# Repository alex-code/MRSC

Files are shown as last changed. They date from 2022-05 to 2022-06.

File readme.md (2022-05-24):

# **M**odel **R**ailway **S**ervo **C**ontroller

Control points, semaphore signals and other accessories using servos.

A demo video can be found here, https://www.youtube.com/watch?v=__FOfBjZpas

| :warning: | I'm a C++ hobbyist (Not a pro) and this is a personal project I've shared that will require some tinkering knowledge. While this has worked for me results may vary and you might need to modify the code.| :warning: |
|--|--|--|

| :information_source: | This was developed using Visual Studio Code and PlatformIO but should be Arduino IDE compatible. | :information_source: |
|--|--|--|

There's 4 types that have different options
- Point - Has 4 speed options
- Semaphore Signal - Can simulate drop bounce and pull up hesitation
- Sweep - Has 4 speed options (Can be used for gates)
- On\Off - Can be used with N Channel mosfets

Parts:
- Arduino UNO
- LCD Keypad Shield (16x2) (I used this https://www.dfrobot.com/product-51.html)
- MCP23017 I/O Port Expander (I used these https://www.dfrobot.com/product-2002.html)
- PCA9685 PWM Servo Driver

Switches can be ON-ON or ON-OFF, they just need to be latching.

I used SG90 servos as they're cheap and common.

## Config

By default the code is setup to handle 4 MCP23017 boards (addressed as 0x20, 0x21, 0x22 & 0x23) and 4 PCA9685 boards (addressed as 0x40, 0x41, 0x42, 0x43).

If the Keypad you have doesn't work you'll need to check the resistance values as these may vary between manufactures.

# Wiring

To make a simpler install I used MCP23017 & PCA9685 boards with pre-soldered headers.

The MCP23017 expanders are set to input pullups so switches need connecting to GND and one of the input pins.

Unless your boards have DIP switches to change the I2C addresses you'll need to do a bit of soldering.

The boards can then be chained with the SDA & SCL pins on the Uno.

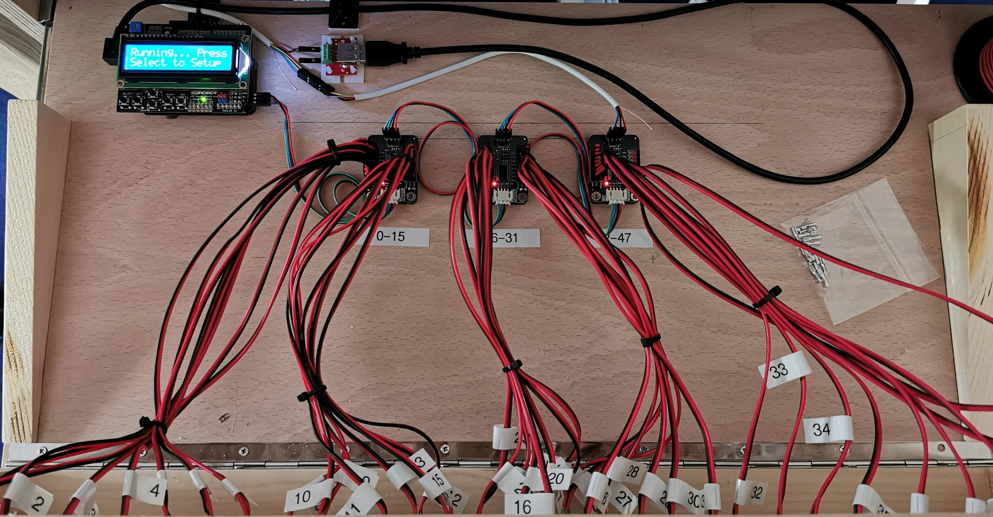
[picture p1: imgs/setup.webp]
My setup


# Servo Numbering

Boards are paired by the order of the addresses in the array.
e.g
```cpp
// MCP's
const uint8_t MCP_ADDRESSES[BOARD_COUNT] = { 0 /* 0x20 */, 1 /* 0x21 */ };
// PCA's'
const uint8_t PCA_ADDRESSES[BOARD_COUNT] = { 0x40, 0x41 }; 
```
The first `MCP` and `PCA` pair will be 0-15 and the second  pair will be 16-31.

# Servo Setup

Servos are a little tricky to setup as the position is unknown to the controller so you'll need to center the servo first (minus the control arm).

- Press *SELECT* on the keypad to start setup.
- You'll first be prompted to select the servo number, use the *UP*/*DOWN* buttons to scroll through the numbers. Press *SELECT* to confirm.
- Press *SELECT* on the first option **Setup/Change**.
- The type can now be selected, **Point**, **Semaphore**, **Sweep**, or **On\Off**. Use the *UP*/*DOWN* buttons to go through the menu options and press *SELECT* on the type you want.
- The servo will now centre.
- After centring you can now fit the arm and the piano wire.
  - For points the arm should be vertical.
  - For semaphore signals the arm should be horizontal.
- You can now set the limits, use the *LEFT*/*RIGHT* buttons to jog the servo in the first direction. When happy with the amount of pressure press *SELECT*. Now go in the opposite direction to set the second limit. Press *SELECT* to confirm.
- You'll then be prompted if the limits are correct. The switch can be toggled at this stage to test, if they are then just press *SELECT* otherwise using the *UP*/*DOWN* buttons you can scroll to **No** and press *SELECT* to go through the limit setup again.
- You'll now be prompted if you want to change the direction the servo operates with the switch. Use *UP*/*DOWN* to change and press *SELECT* to confirm.
- **Point Type**
  - You can now select 1 of 4 speeds. Use the *UP*/*DOWN* buttons to scroll through the speeds. The switch can also be tested so you can give each speed a try. Press *SELECT* to confirm.
- **Semaphore Type**
  - Select if you want to simulate a semaphore signal bounce on drop. You can use the switch the test. Press *SELECT* to confirm.
  - Select if you want to simulate a semaphore hesitate on pull up. You can use the switch the test. Press *SELECT* to confirm.
- **Sweep Type**
  - You can now select 1 of 4 speeds. Use the *UP*/*DOWN* buttons to scroll through the speeds. The switch can also be tested so you can give each speed a try. Press *SELECT* to confirm.
- The display will then read **Setup Complete** before prompting if you want to setup another servo.
If you select **Yes** the servo select will auto increment to the next number so you can just press *SELECT* to continue or use the *UP*/*DOWN* buttons to select a different servo.

## Existing
If you need to change an existing servo.
- Press *SELECT* on the keypad to start setup.
- You'll first be prompted to select the servo number, use the *UP*/*DOWN* buttons to scroll through the numbers. Press *SELECT* to confirm.
- Press *SELECT* on the first option **Setup/Change**.
- If the servo has a previous setup you'll be prompted if you want to overwrite. This allows you to change the type and reset the limits.
- Depending on the type you'll then be able to change the options.

# Servo Mounts

Servos can be mounted with which ever method suits you best but I've included some STL files that can be used to 3D print underside and topside servo mounts (underside needs a 10mm hole for the shaft).

| :warning: | I model in N Gauge so they're sized for that, if you plan on using them for OO/HO they may need tweaking | :warning: |
|--|--|--|

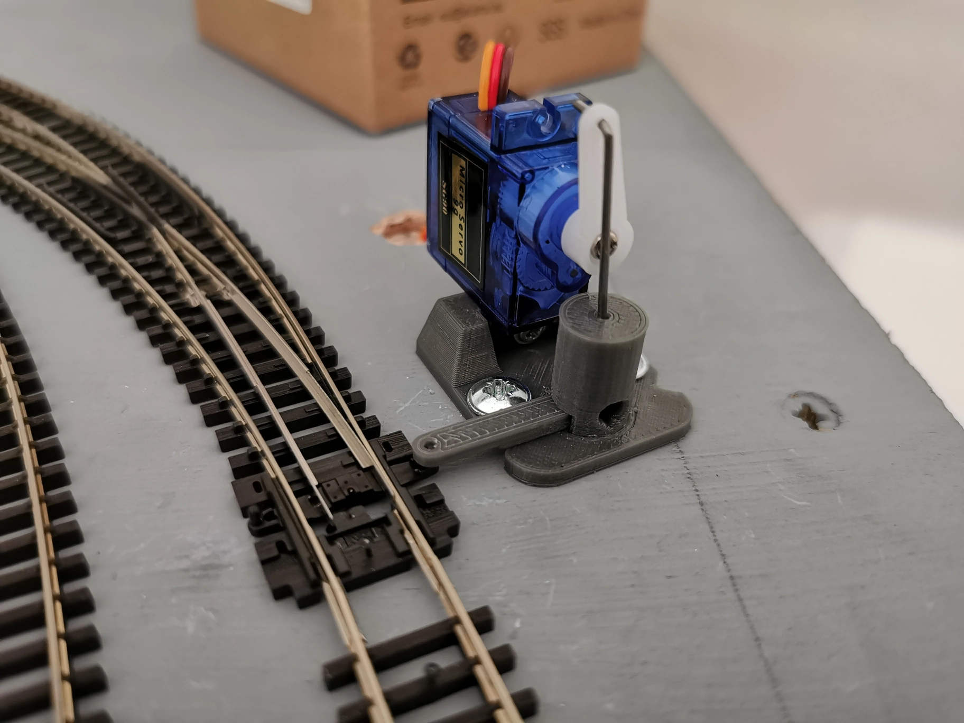
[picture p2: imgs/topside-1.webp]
Topside mount

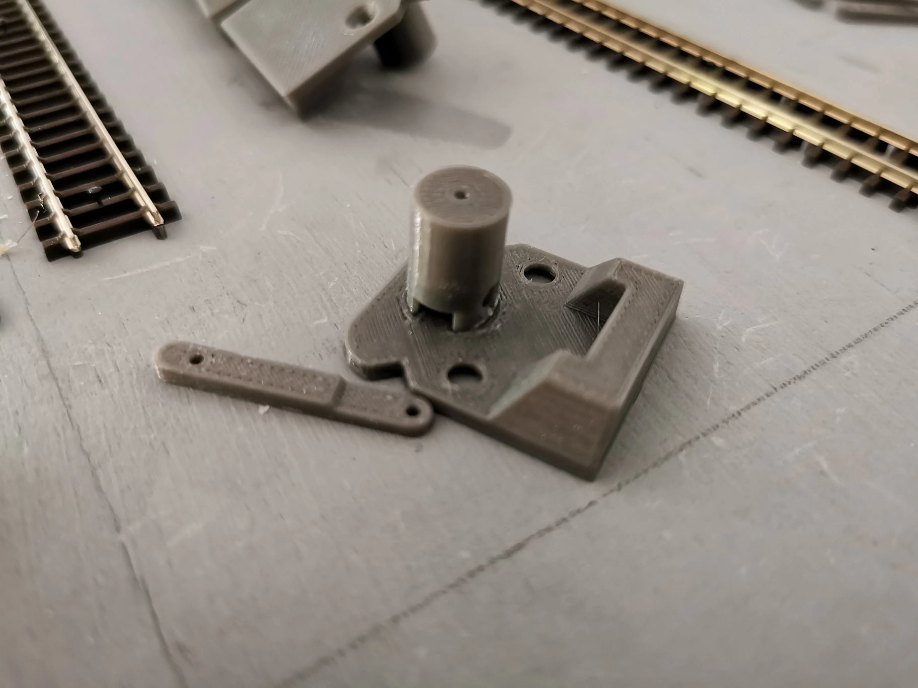
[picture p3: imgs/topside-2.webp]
Topside mount

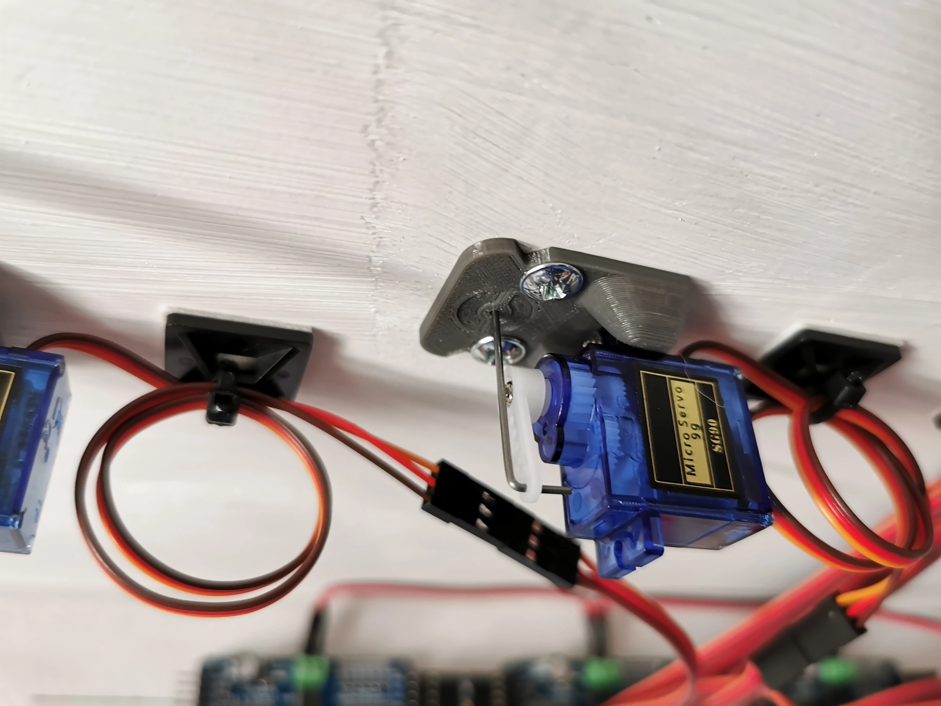
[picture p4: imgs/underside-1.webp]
Underside mount

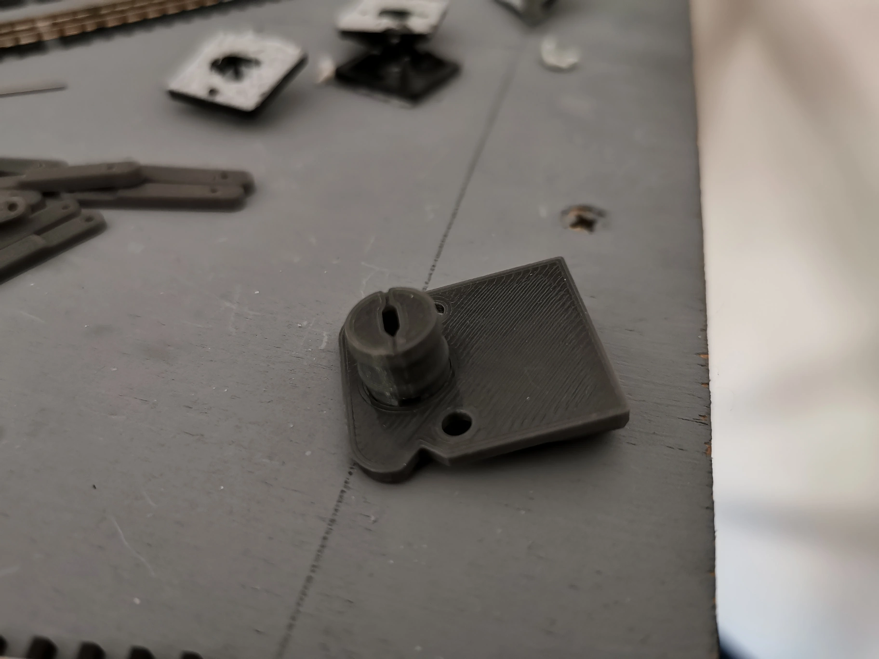
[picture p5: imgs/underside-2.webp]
Underside mount


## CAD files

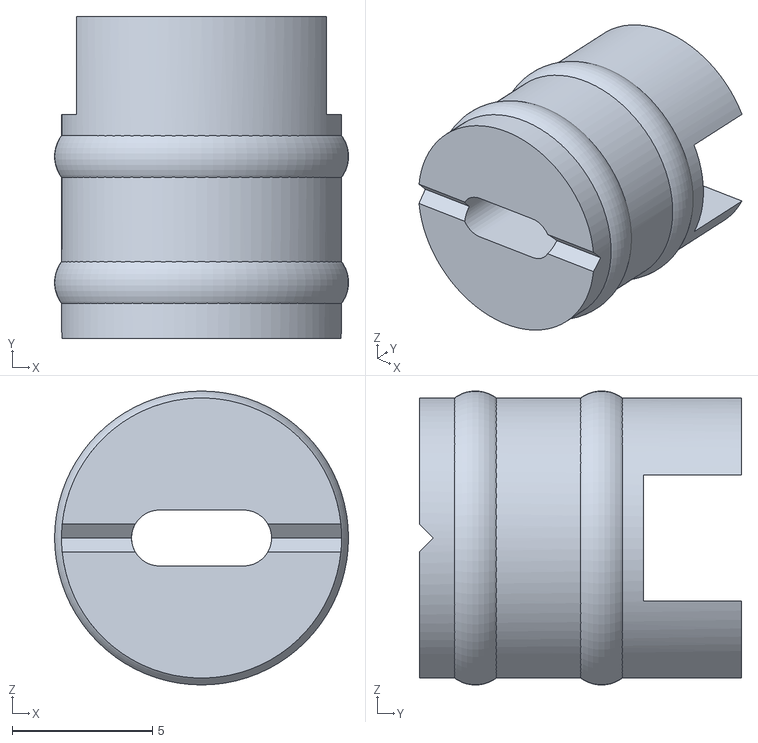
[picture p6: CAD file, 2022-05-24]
3d/Underside Shaft.stl
10.5 x 11.5 x 10.5

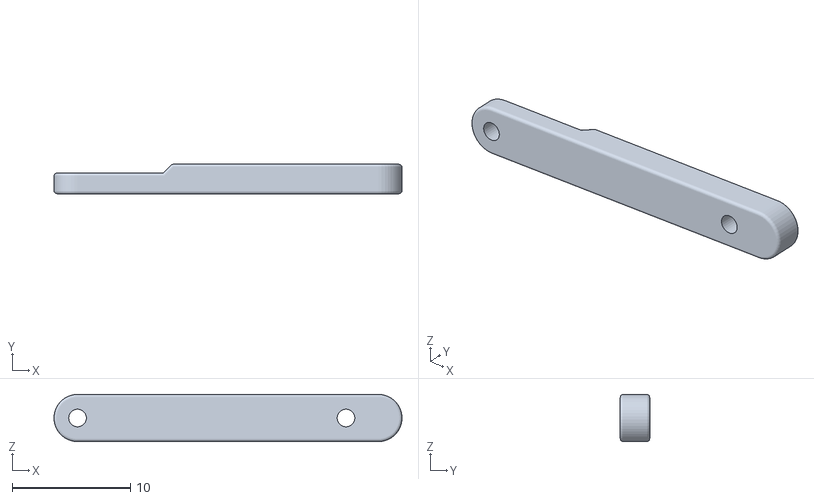
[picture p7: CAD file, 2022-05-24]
3d/Topside Rod.stl
29.5 x 2.50 x 4.00

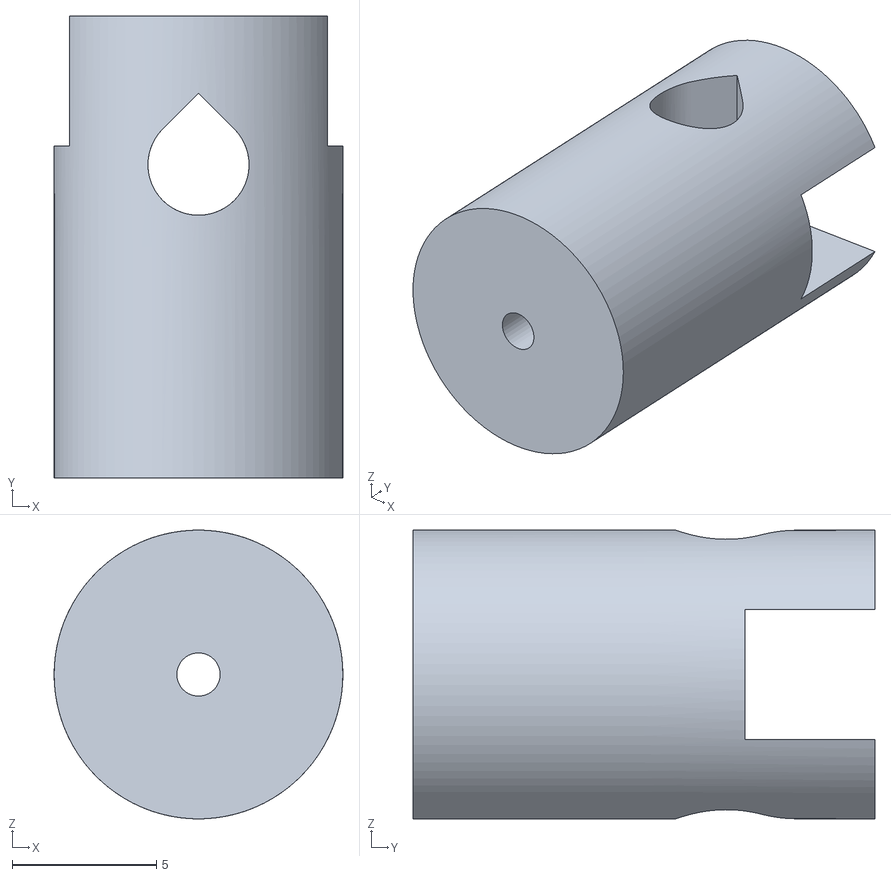
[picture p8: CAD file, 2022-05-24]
3d/Topside Shaft.stl
10.0 x 16.0 x 10.0

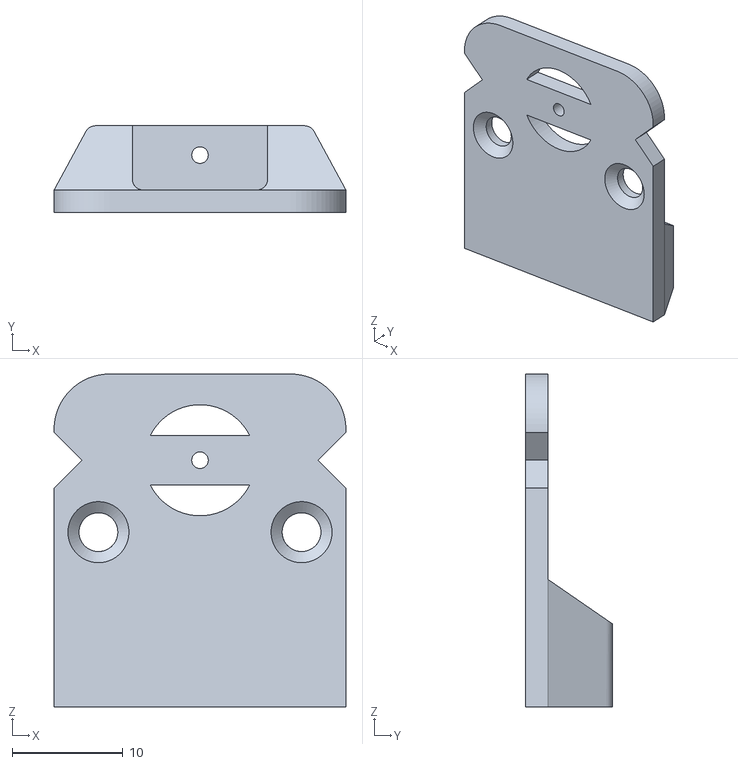
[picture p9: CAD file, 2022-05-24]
3d/Servo Mount.stl
26.3 x 7.80 x 30.0

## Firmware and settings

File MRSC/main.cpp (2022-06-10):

#include <Arduino.h>
#include <EEPROM.h>
#include <Wire.h>
#include <LiquidCrystal.h>
#include <Adafruit_MCP23017.h>
#include <Adafruit_PWMServoDriver.h>

// How many MCP23017 & PCA9685 boards are connected, needs to be an equal amount
const uint8_t BOARD_COUNT = 4;

// Keypad & Display
const uint8_t KEYPAD_PIN = 0; // A0

// MCP's - Addresses start from the base 0x20
const uint8_t MCP_ADDRESSES[BOARD_COUNT] = { 0 /* 0x20 */, 1 /* 0x21 */, 2 /* 0x22 */, 3 /* 0x23 */ };

// PCA Servo Drivers
const uint16_t SERVO_MIN = 90;
const uint16_t SERVO_MAX = 440;
const uint8_t SERVO_FREQ = 50;
const uint8_t PCA_ADDRESSES[BOARD_COUNT] = { 0x40, 0x41, 0x42, 0x43 };

// Board group
struct {
  Adafruit_MCP23017 *mcp = nullptr; // MCP23017
  Adafruit_PWMServoDriver *pca = nullptr; // PCA9685
  uint16_t states = 0;
} boards[BOARD_COUNT];

enum class Type : uint8_t {
  POINT,      // Full sweep from limit to limit
  SEMAPHORE,  // Full sweep from limit to limit with optional simulation of semaphore drop bounce and pull up hesitate
  SWEEP,      // Similar to POINT but with different speeds, can be used for gates etc.
  ONOFF       // 0v or 5v to allow trigger of other components, e.g N-Channel MOSFET
};

// These are ms delay times between each degree move
uint8_t pointSpeeds[] = { 25, 30, 35, 40 };
uint8_t sweepSpeeds[] = { 15, 25, 35, 45 };

// Servo config
struct {
  uint8_t limit1; // Limit 1
  uint8_t limit2; // Limit 2
  Type type;
  bool swap; // A convenience option, can swap the direction without needing to change wires
  uint8_t speed;
  bool hesitate; // Simulate hesitate
  bool bounce; // Simulate bounce
  uint32_t unused; // Bit of space in case there's future updates
} servos[BOARD_COUNT * 16];

#define MENUSIZE(items) sizeof(items) / 16
const char yesNoMenu[][16] PROGMEM = { "Yes", "No" };
const char servoSetupMenu[][16] PROGMEM = { "Setup/Change", "Swap Direction", "Centre", "Cancel" };
const char servoSetupTypeMenu[][16] PROGMEM = { "Point", "Semaphore", "Sweep", "On/Off" };
const char servoPointSpeedMenu[][16] PROGMEM = { "Speed 1", "Speed 2", "Speed 3", "Speed 4" };
const char servoSweepSpeedMenu[][16] PROGMEM = { "Speed 1", "Speed 2", "Speed 3", "Speed 4" };

uint8_t board = 0;
uint8_t pin = 0;
void checkForChange();

namespace Keypad {
  enum class Key : uint8_t {
    NONE    = 0,
    LEFT    = 1,
    RIGHT   = 2,
    UP      = 3,
    DOWN    = 4,
    SELECT  = 5
  };

  Key getKey(bool blocking = true) {
    Key key = Key::NONE;
    uint16_t adc;

    do {
      adc = 0;
      for (uint8_t i = 0; i < 5; i++) {
        adc += analogRead(KEYPAD_PIN);
        delay(5);
      }
      adc /= 5;

      if (adc < 50) {
        key = Key::RIGHT;
      } else if (adc < 250) {
        key = Key::UP;
      } else if (adc < 450) {
        key = Key::DOWN;
      } else if (adc < 650) {
        key = Key::LEFT;
      } else if (adc > 800 && adc < 850) {
        key = Key::SELECT;
      }
    } while (blocking && adc < 1000);

    return key;
  }
}

namespace Display {
  LiquidCrystal LCD(8, 9, 4, 5, 6, 7);

  void initialize() {
    LCD.begin(16, 2);
  }

  auto _change = [](int8_t) { };
  template<typename onChange = decltype(_change)>
  uint8_t showMenu(const __FlashStringHelper *title, const char menu[][16], uint8_t count, int8_t index = 0, onChange change = _change) {
    Keypad::Key oldKey = Keypad::Key::SELECT;
    Keypad::Key newKey = Keypad::Key::NONE;

    count--;
    if (index > count) {
      index = count;
    }

    LCD.clear();
    LCD.print(title);
    LCD.setCursor(0, 1);
    LCD.print((__FlashStringHelper*)&menu[index]);

    uint8_t len = strlen_P((const char*)title);
    int8_t scroll = len - 16;
    uint32_t wait = millis() + 1000;
    uint8_t i = 0;
    bool ltr = true;

    delay(100);

    do {
      if (len > 16 && millis() > wait) { // Scroll the title
        ltr ? i++ : i--;
        if (i == scroll || i == 0) { // Change scroll direction
          ltr = !ltr;
          wait = millis() + 1000; // Wait for 1 second before starting to scroll again
        } else {
          wait = millis() + 500;
        }
        
        LCD.setCursor(0, 0);
        LCD.print((const __FlashStringHelper *)((char*)title + i));
      }

      newKey = Keypad::getKey();
      if (oldKey != newKey) {
        if (newKey == Keypad::Key::DOWN) {
          if (++index > count) {
            index = 0;
          }
        } else if (newKey == Keypad::Key::UP) {
          if (--index < 0) {
            index = count;
          }
        }
        LCD.setCursor(0, 1);
        LCD.print((__FlashStringHelper*)&menu[index]);
        LCD.print(F("                "));

        oldKey = newKey;

        if (oldKey == Keypad::Key::NONE) {
          change(index);
        }
      }

      checkForChange();
    } while (newKey != Keypad::Key::SELECT);

    return index;
  }
}

namespace Switches {
  Adafruit_MCP23017* initialize(uint8_t address) {
    Adafruit_MCP23017 *mcp = new Adafruit_MCP23017;
    mcp->begin(address);
    // We want input pullups on all 16 pins
    for (uint8_t i = 0; i < 16; i++) {
      mcp->pullUp(i, HIGH);
    }

    return mcp;
  }

  bool hasChanged(uint8_t &board, uint8_t &pin) {
    for (uint8_t b = 0; b < BOARD_COUNT; b++) { // Loop the MCP23017 boards
      if (boards[b].mcp == nullptr) { // No MCP board to query
        continue;
      }
      uint16_t pins = boards[b].mcp->readGPIOAB();
      if (pins == boards[b].states) { // Any changes?
        continue;
      }
      for (uint8_t p = 0; p < 16; p++) { // Check all 16 pins
        if (bitRead(boards[b].states, p) != bitRead(pins, p)) {
          bitToggle(boards[b].states, p);
          board = b;
          pin = p;
          return true;
        }
      }
    }

    return false;
  }
}

namespace Servos {
  Adafruit_PWMServoDriver* initialize(uint8_t address) {
    Adafruit_PWMServoDriver *pca = new Adafruit_PWMServoDriver(address);

    pca->begin();
    pca->setOscillatorFrequency(27000000);
    pca->setPWMFreq(SERVO_FREQ);

    return pca;
  }

  uint8_t select(uint8_t &board, uint8_t &pin, uint8_t start = 0) {
    Display::LCD.clear();
    Display::LCD.print(F("Select Servo #"));
    
    int8_t servo = start;

    Display::LCD.setCursor(0, 1);
    Display::LCD.print(servo);

    Keypad::Key key;
    uint32_t held = 0;    

    do {
      key = Keypad::getKey(false);
      if (held == 0 || millis() > held + 500) {
        if (key == Keypad::Key::DOWN) {
          if (--servo < 0) {
            servo = (BOARD_COUNT * 16) - 1;
          }
          Display::LCD.setCursor(0, 1);
          Display::LCD.print(servo);
          Display::LCD.print(F("  "));
        } else if (key == Keypad::Key::UP) {
          if (++servo > (BOARD_COUNT * 16) - 1) {
            servo = 0;
          }
          Display::LCD.setCursor(0, 1);
          Display::LCD.print(servo);
          Display::LCD.print(F("  "));
        }
        if (held == 0) {
          held = millis();
        } else {
          delay(100);
        }
      }
      if (key == Keypad::Key::NONE) {
        held = 0;
      }
    } while (key != Keypad::Key::SELECT);

    board = servo / 16;
    pin = servo % 16;

    delay(100);

    return servo;
  }

  void setAngle(uint8_t board, uint8_t pin, uint8_t angle, uint16_t msDelay, bool off) {
    uint16_t pulseLength = map(angle, 0, 180, SERVO_MIN, SERVO_MAX);
    boards[board].pca->setPWM(pin, 0, pulseLength);
    delay(msDelay);
    if (off) { // There's no real load on the servo so we can disable it after it's moved. Saves a bit of power and stops it hunting
      boards[board].pca->setPWM(pin, 0, 4096);
    }
  }

  void sweep(uint8_t board, uint8_t pin, uint8_t from, uint8_t to, uint8_t delay) {
    if (from < to) {
      for (uint8_t i = from; i <= to; i++) {
        setAngle(board, pin, i, delay, i == to);
      }
    } else {
      for (uint8_t i = from; i >= to; i--) {
        setAngle(board, pin, i, delay, i == to);
      }
    }
  }

  void change(uint8_t board, uint8_t pin, uint8_t servo) {
    if (bitRead(boards[board].states, pin) ^ servos[servo].swap) {
      switch (servos[servo].type) {
        case Type::POINT: {
          sweep(board, pin, servos[servo].limit1, servos[servo].limit2, pointSpeeds[servos[servo].speed]);
        } break;
        case Type::SEMAPHORE: {
          // TODO, speed on semaphores?
          sweep(board, pin, servos[servo].limit1, servos[servo].limit2, 20);
          if (servos[servo].bounce) {
            int8_t bounce = (servos[servo].limit2 - servos[servo].limit1) / 5;
            sweep(board, pin, servos[servo].limit2, servos[servo].limit2 - bounce, 15);
            sweep(board, pin, servos[servo].limit2 - bounce, servos[servo].limit2, 15);
            bounce /= 2;
            sweep(board, pin, servos[servo].limit2, servos[servo].limit2 - bounce, 15);
            sweep(board, pin, servos[servo].limit2 - bounce, servos[servo].limit2, 15);
          }
        } break;
        case Type::SWEEP: {
          sweep(board, pin, servos[servo].limit1, servos[servo].limit2, sweepSpeeds[servos[servo].speed]);
        } break;
        case Type::ONOFF: {
          boards[board].pca->setPWM(pin, 4096, 0);
        } break;
      }
    } else {
      switch (servos[servo].type) {
        case Type::POINT: { // TODO hesitate for points too, simulate lever pull?
          sweep(board, pin, servos[servo].limit2, servos[servo].limit1, pointSpeeds[servos[servo].speed]);
        } break;
        case Type::SEMAPHORE: {
          if (servos[servo].hesitate) {
            int8_t half = (servos[servo].limit2 - servos[servo].limit1) / 2;
            sweep(board, pin, servos[servo].limit2, servos[servo].limit2 - half, 35);
            delay(200);
            sweep(board, pin, servos[servo].limit2 - half, servos[servo].limit1, 35);
          } else {
            sweep(board, pin, servos[servo].limit2, servos[servo].limit1, 35);
          }
        } break;
        case Type::SWEEP: {
          sweep(board, pin, servos[servo].limit2, servos[servo].limit1, sweepSpeeds[servos[servo].speed]);
        } break;
        case Type::ONOFF: {
          boards[board].pca->setPWM(pin, 0, 4096);
        } break;
      }
    }
  }

  void jog(uint8_t limit, uint8_t board, uint8_t pin, uint8_t &angle) {
    Display::LCD.clear();
    Display::LCD.print(F("Setup Limit "));
    Display::LCD.print(limit);
    Display::LCD.setCursor(0, 1);
    Display::LCD.print(F("Use L/R to Jog"));

    setAngle(board, pin, angle, 100, true);

    Keypad::Key key;
    uint32_t held = 0;
    do {
      key = Keypad::getKey(false);
      if (!held || millis() > held + 500) {
        if (key == Keypad::Key::LEFT) {
          setAngle(board, pin, --angle, 100, true);
        } else if (key == Keypad::Key::RIGHT) {
          setAngle(board, pin, ++angle, 100, true);
        }
        if (!held) {
          held = millis();
        }
      }
      if (key == Keypad::Key::NONE) {
        held = 0;
      }
    } while (key != Keypad::Key::SELECT);

    delay(100);
  }

  void setup(uint8_t board, uint8_t pin, uint8_t servo) {
    if ((uint8_t)servos[servo].type == 0xFF || !Display::showMenu(F("Existing Setup - Overwrite?"), yesNoMenu, MENUSIZE(yesNoMenu), 1)) {
      servos[servo].type = (Type)Display::showMenu(F("Setup Type"), servoSetupTypeMenu, MENUSIZE(servoSetupTypeMenu));
      // Defaults
      servos[servo].swap = false;
      servos[servo].speed = 0;
      servos[servo].hesitate = false;
      servos[servo].bounce = false;

      if (servos[servo].type != Type::ONOFF) {
        do {
          Display::LCD.clear();
          Display::LCD.print(F("Centring"));
          delay(1000);

          servos[servo].limit1 = 90;
          jog(1, board, pin, servos[servo].limit1);

          servos[servo].limit2 = 90;
          jog(2, board, pin, servos[servo].limit2);
        } while (Display::showMenu(F("Limits Correct? - Test Switch"), yesNoMenu, MENUSIZE(yesNoMenu)) == 1);
      }
    }

    Display::showMenu(F("Swap Direction? - Test Switch"), yesNoMenu, MENUSIZE(yesNoMenu), 1, [&](uint8_t selected) {
      servos[servo].swap = !selected;
    });

    switch (servos[servo].type) {
      case Type::POINT: {
        Display::showMenu(F("Select Speed - Test Switch"), servoPointSpeedMenu, MENUSIZE(servoPointSpeedMenu), 0, [&](uint8_t selected) {
          servos[servo].speed = selected;
        });
      } break;
      case Type::SEMAPHORE: {
        Display::showMenu(F("Simulate Bounce? - Test Switch"), yesNoMenu, MENUSIZE(yesNoMenu), 0, [&](uint8_t selected) {
          servos[servo].bounce = !selected;
        });
        Display::showMenu(F("Simulate Hesitate? - Test Switch"), yesNoMenu, MENUSIZE(yesNoMenu), 0, [&](uint8_t selected) {
          servos[servo].hesitate = !selected;
        });
      } break;
      case Type::SWEEP: {
        Display::showMenu(F("Select Speed - Test Switch"), servoSweepSpeedMenu, MENUSIZE(servoSweepSpeedMenu), 0, [&](uint8_t selected) {
          servos[servo].speed = selected;
        });
      } break;
      default: break;
    }

    Display::LCD.clear();
    Display::LCD.print(F("Setup Complete"));
    delay(1000);
  }
}

void running() {
  Display::LCD.clear();
  Display::LCD.print(F("Running... Press"));
  Display::LCD.setCursor(0, 1);
  Display::LCD.print(F("Select to Setup"));
}

void setup() {
  Serial.begin(9600);

  Wire.begin();
  Wire.setClock(400000);

  EEPROM.get(0, servos);
  Display::initialize();

  auto detect = [](uint8_t addr) -> bool {
    Wire.beginTransmission(addr);
    return Wire.endTransmission() == 0;
  };
  
  for (uint8_t c = 0; c < BOARD_COUNT; c++) {
    // Setup the MCP23017 & PCA9685 boards
    if (detect(MCP23017_ADDRESS | MCP_ADDRESSES[c]) && detect(PCA_ADDRESSES[c])) {
      #if __cplusplus >= 201402L
      boards[c] = {
        Switches::initialize(MCP_ADDRESSES[c]),
        Servos::initialize(PCA_ADDRESSES[c]),
      };
      #else
      boards[c].mcp = Switches::initialize(MCP_ADDRESSES[c]);
      boards[c].pca = Servos::initialize(PCA_ADDRESSES[c]);
      #endif
      // Get current switch positions
      boards[c].states = boards[c].mcp->readGPIOAB();
    }
  }

  running();
}

// cppcheck-suppress unusedFunction
void loop() {
  if (Keypad::getKey() == Keypad::Key::SELECT) {
    uint8_t servo = 0;
    uint8_t menu = UINT8_MAX;
    do {
      servo = Servos::select(board, pin, servo);
      if (menu == UINT8_MAX) {
        menu = Display::showMenu(F("Setup Servos"), servoSetupMenu, MENUSIZE(servoSetupMenu));
      }
      if (menu == 0) { // Setup
        Servos::setup(board, pin, servo);
        EEPROM.put(0, servos);
        menu = Display::showMenu(F("Setup/Change Another?"), yesNoMenu, MENUSIZE(yesNoMenu));
        servo++; // If we continue to setup another then auto inc the servo #
      } else if (menu == 1) { // Swap
        servos[servo].swap = !servos[servo].swap;
        EEPROM.put(0, servos);
        Display::LCD.clear();
        Display::LCD.print(F("Swapped"));
        delay(1000);
      } else if (menu == 2) { // Centre
        Servos::setAngle(board, servo, 90, 100, true);
      }
    } while (menu == 0);
    
    running();
  }

  checkForChange();
}

void checkForChange() {
  if (Switches::hasChanged(board, pin)) {
    // TODO, sleep and wake PWM boards?
    uint8_t servo = (board * 16) + pin;
    if ((uint8_t)servos[servo].type != 0xFF) { // Do we have a valid type? Only change if so. EEPROM defaults are 0xFF
      Servos::change(board, pin, servo);
    }
  }
}

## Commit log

2022-05-26 i2c detect bugfix
    The Adafruit MCP23017 class doesn't take the direct address but uses a base of `0x20`. This was missed on the detect.
    [main.cpp]
2022-06-10 Possible fix for incorrect SELECT detect
    The `LEFT` key is close in the analog range to `SELECT` so quick presses of `LEFT` could be detected as `SELECT`.
    Added sampling and changed the range check.
    [main.cpp]
